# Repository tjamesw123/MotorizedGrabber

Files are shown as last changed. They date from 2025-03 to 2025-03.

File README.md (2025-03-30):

# MotorizedGrabber
3d models, custom circuit board, design and parts list for a motorized grabber design

# Grabber Shopping List

2 mm outer thickness with 22 mm inner diameter alumuinum pipe, 2 meters 

3d printer and filament, carbon fiber PLA was used for this grabber but normal PLA should still work with possibly some tweaks to the models or maybe non at all as Carbon Fiber PLA and PLA have similar print characteristics
(Note that a sleve was used for fitting the adapter to the alumnium grabber pipe better after the lathe was used to trim the part till it fit with the alumium pipe, there is almost certainly another way to fit the aluminum pipe and the part together without such equipment. I would suggest tuning the fitting parts of the prints inner and outer diameter sizes till you can print a part that fits well with the aluminium pipe without any trim)

Drill Batterys and Charger https://www.amazon.com/dp/B07X2V5116/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

Round Head Machine Screw, 8-32-Inch x 1-Inch, 2 of them https://www.amazon.com/dp/B00843ER7W?ref_=cm_sw_r_cp_ud_dp_5XYYPG3079ASXCVBMPT5

Small Screws https://www.amazon.com/dp/B078ZVLFWY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

Micro Limit Switch	https://www.amazon.com/dp/B07X142VGC/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 , I got the 10 pack of these but most limit switches will do as you only need one of them for the limiter

SPDT Push Button Switches https://www.digikey.com/en/products/detail/e-switch/700SP7B10M2QEH/502058 , I bought 4 when making it in case I messed up 2 but you only need 2 for the design

Custom Circuit Board for Grabber , The gerber files are in the repo, I used PCBWay for ordering the boards, you do have to mininum order 10 for 20 dollars but for this project it made soldering way easier and much more reliable then soldering directly to the pins.

A fair amount of 22 gage wire, I made an attempt at using quick connects to make the battery connection to the switches easier to disconnect but the current space issues make such things mildly difficult so you can just directly wire up the grabber and desolder for repairs. Annoying but with the space constraints it made sense at the time.

There are about 4 separate runs of wire you will have to run other then the wires built into the linear actuator
There are circuit diagrams that you can view from the photo section of the layout of the switch board or if you feel like not using it, it's going to tell you exactly how you have to run things.

Grabber 48"	https://www.amazon.com/dp/B000RUKZNU?ref=ppx_yo2ov_dt_b_fed_asin_title&th=1 , this is the grabber that you need to basically need to cut and then combined with the other parts in this design
Or
Grabber 36" https://www.amazon.com/dp/B0000V0AGS/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 , another grabber you can use if you want a shorter grabber for whatever reason, still works out the same for the most part

Battery Prongs	https://www.te.com/en/product-42214-2.html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 , I bought 4 again also because I wanted backups but you only need 2\

Micro Linear Actuator https://www.amazon.com/dp/B0B9JPQDSV?ref=ppx_yo2ov_dt_b_fed_asin_title&th=1, I bought 1 of these
(The gearing here is more aggressive then it needs to be on the 36" grabber but for the 48" it is required to get one of these as the gearing for a faster motor doesn't have enough static friction to keep the spring on the grabber from moving)

### An addendum on the PCB
You technically don't need this thing if your really determined but trust me when I say it really can be scuffed if you don't get this, if you are a beginner solderer I would recommend this and honestly even if your more experienced it just makes the whole circuit a lot neater. Having tiny 22 gage wires running inbetween the pins is messy, I rest my case. I have like 7 spares at this moment in time so if your really determined to not order a fresh batch you can attempt to reach out. The dupes also leave room for failures and they make for ok solder practice boards as well with the number of pins.

The spacing is also tiny there isn't a lot of room in the handle of the grabber so the board just made sense to keep things more neat

## Photos

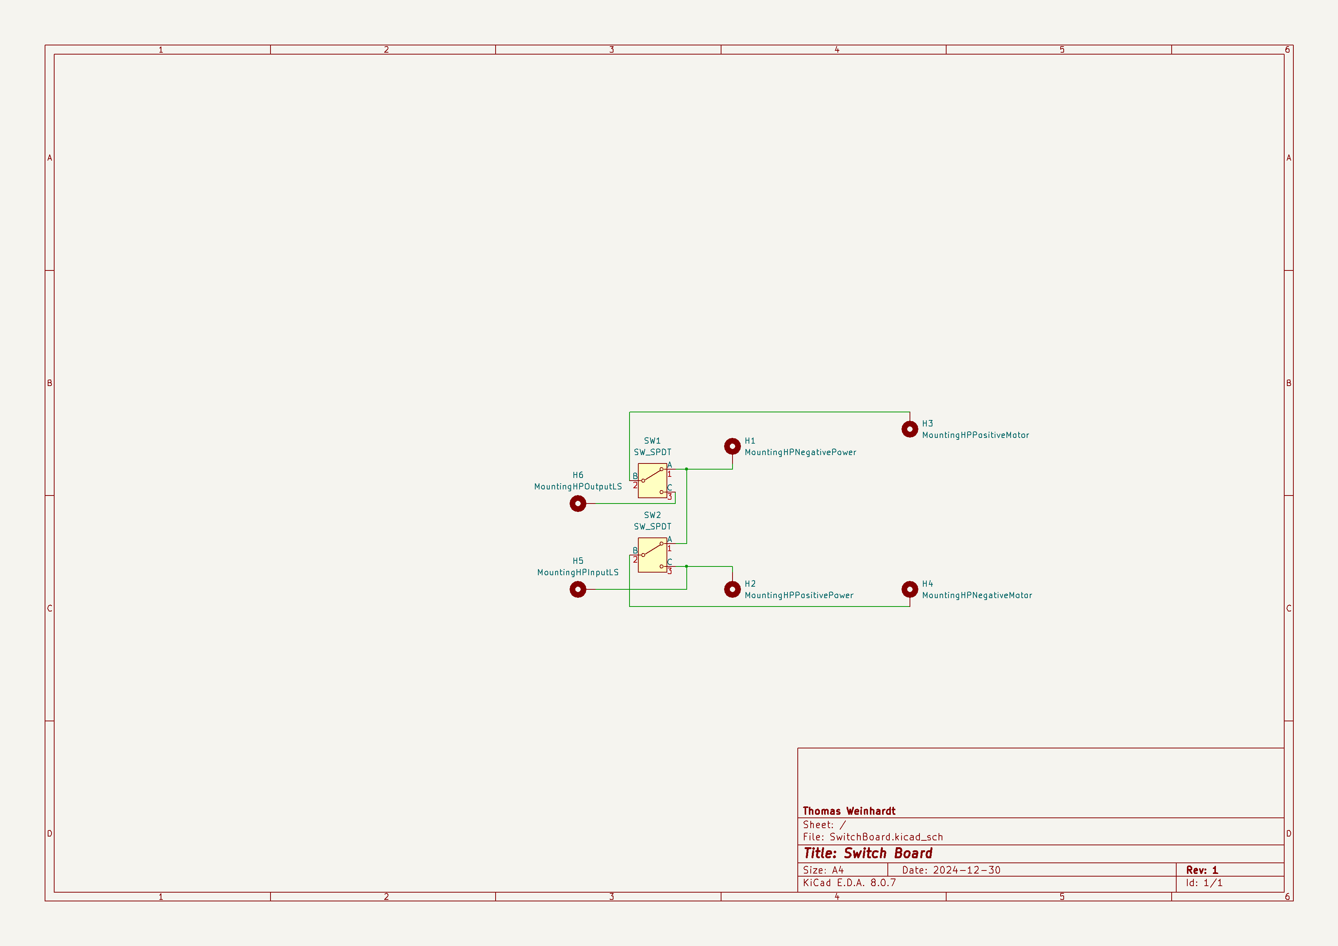
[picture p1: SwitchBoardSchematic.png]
Switch Board Schematic

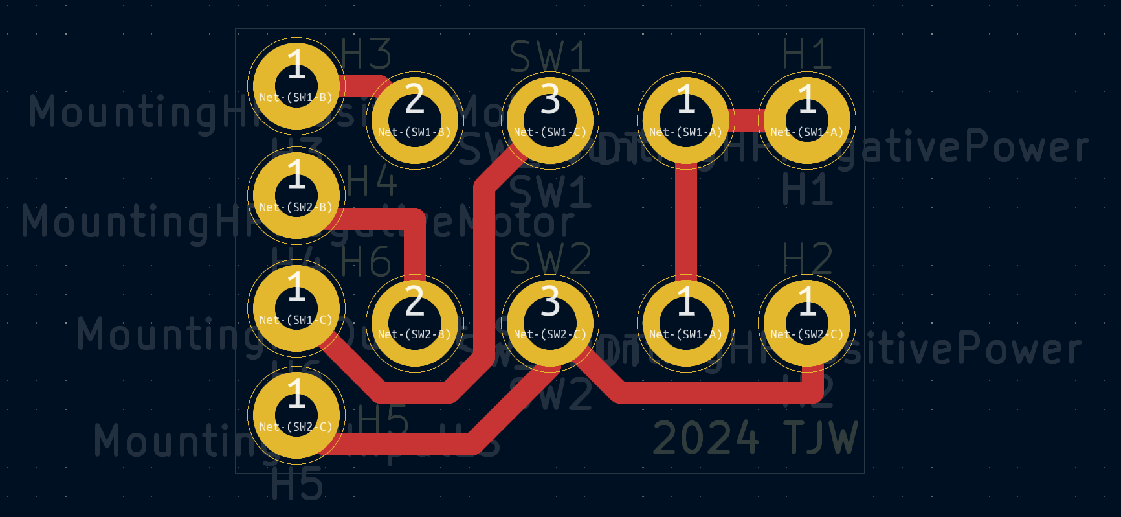
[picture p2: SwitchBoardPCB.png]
Switch Board PCB


(I used KiCAD for the board designing program)
[GerbersAndProductionFiles](SwitchBoard/pcbway_production)
Also use the settings listed in the [GrabberPCBSpecs](GrabberPCBSpecs.pdf)

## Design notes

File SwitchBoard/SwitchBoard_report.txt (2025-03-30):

PCB statistics report
=====================
- Date: 12/30/2024 1:51:36 PM
- Project: SwitchBoard
- Board name: SwitchBoard

Board
-----
- Width: 22.0000 mm
- Height: 15.4000 mm
- Area: 338.8000 mm²

Pads
----
- Through hole: 6
- SMD: 6
- Connector: 0
- NPTH: 0

Vias
----
- Through vias: 0
- Blind/buried: 0
- Micro vias: 0

Components
----------

| | Front Side | Back Side | Total |
|---|---|---|---|
|THT: | 8 | 0 | 8 |
|SMD: | 0 | 0 | 0 |
|Unspecified:  | 0 | 0 | 0 |
|Total: | 8 | 0 | 8 |

Drill holes
-----------

| Count | Shape | X Size | Y Size | Plated | Via/Pad | Start Layer | Stop Layer |
|---|---|---|---|---|---|---|---|
| 6 | Round | 1.8500 mm | 1.8500 mm | PTH | Pad | F.Cu | B.Cu |

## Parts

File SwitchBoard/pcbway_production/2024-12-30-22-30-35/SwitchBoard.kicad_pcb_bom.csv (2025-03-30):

Designator | Quantity | Value | Footprint | Package | MPN | DNP | Mount_Type | Description
SW1, SW2 | 2 | SW_SPDT | SP-7 |  |  |  | tht | Switch, single pole double throw

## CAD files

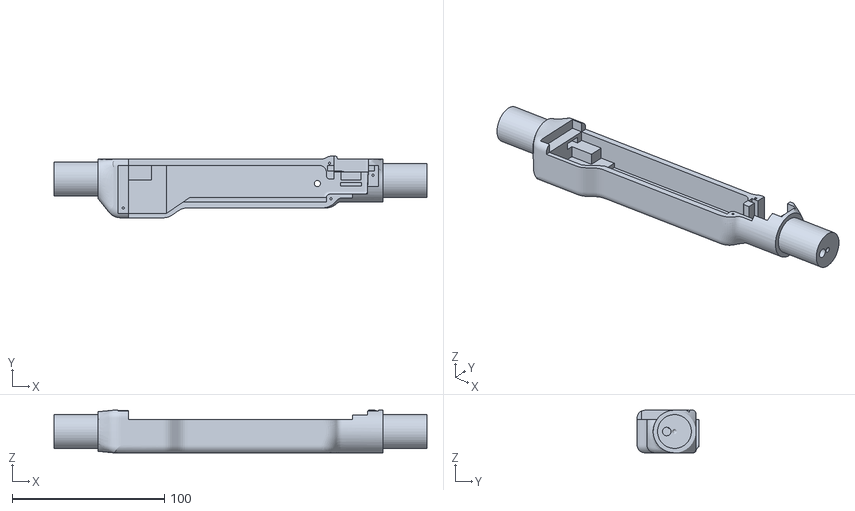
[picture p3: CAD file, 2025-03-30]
PartsFolder/GrabberCasingMain.stl
244.9 x 40.5 x 28.0

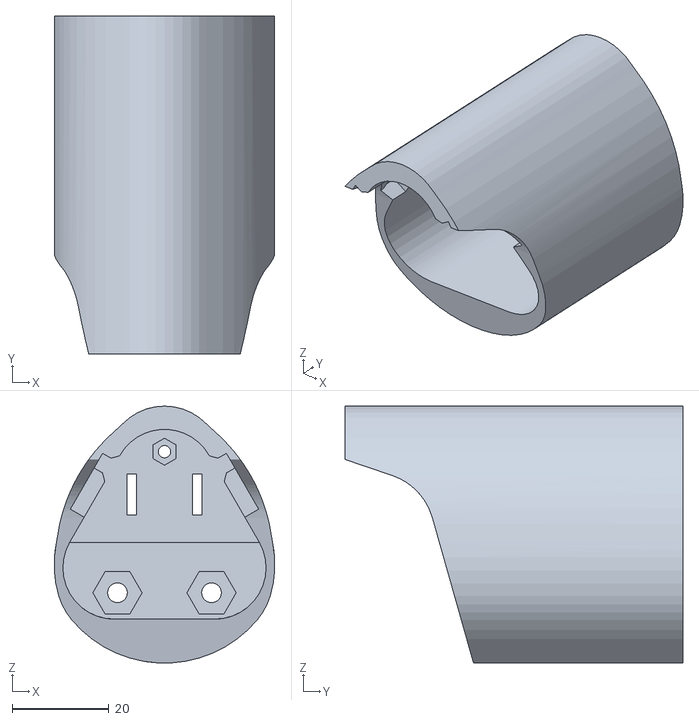
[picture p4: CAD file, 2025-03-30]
PartsFolder/GrabberBatteryHolder.stl
45.5 x 69.7 x 53.0

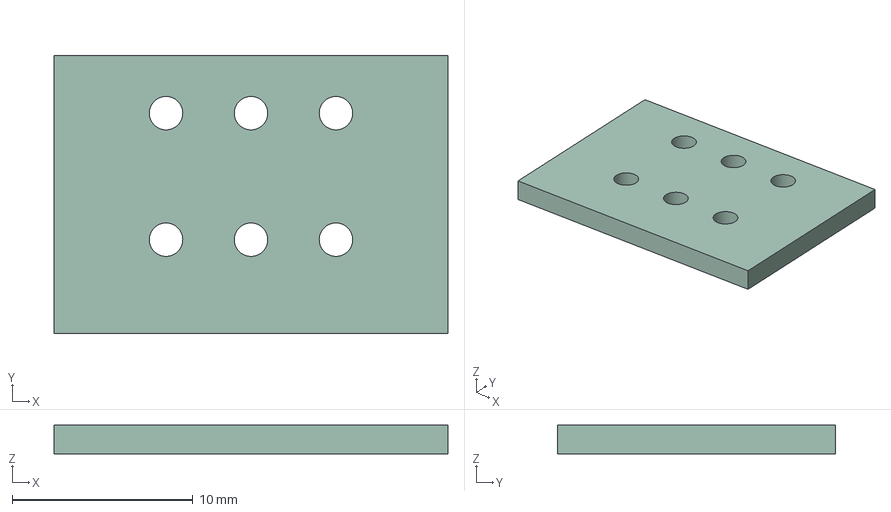
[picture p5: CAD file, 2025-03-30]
SwitchBoard/SwitchBoard.step
21.8 x 15.4 x 1.60 mm

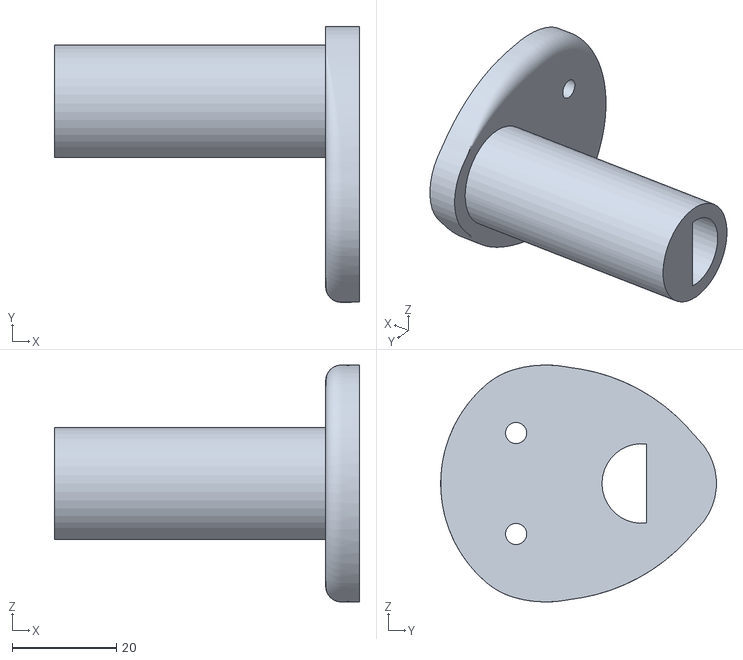
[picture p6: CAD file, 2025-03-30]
PartsFolder/GrabberBatteryCap.stl
58.6 x 53.0 x 45.5

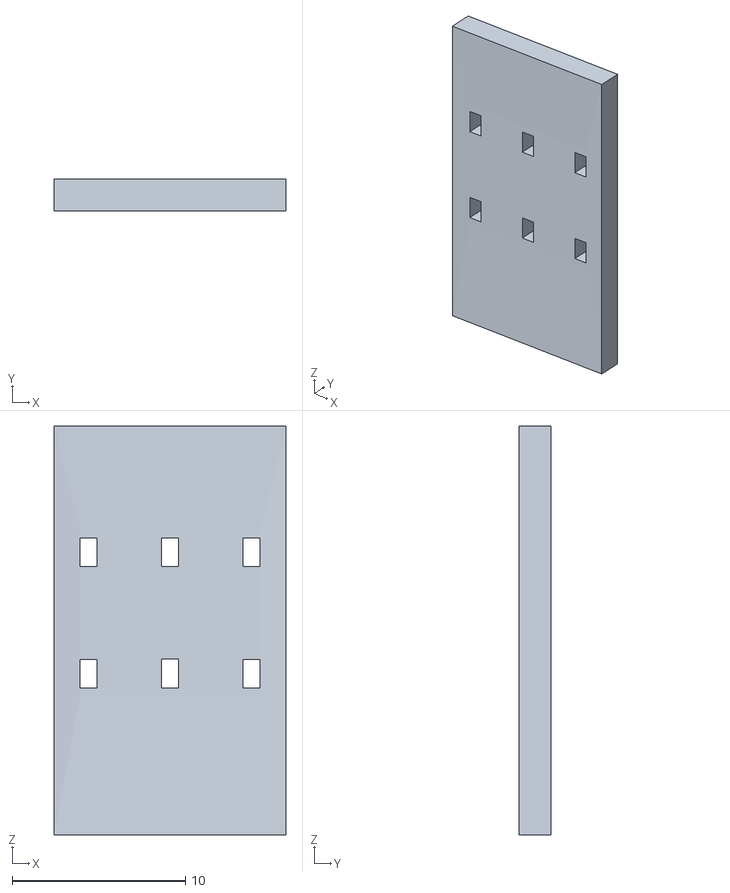
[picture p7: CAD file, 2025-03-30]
PartsFolder/GrabberButtonPlatform.stl
13.4 x 1.82 x 23.6

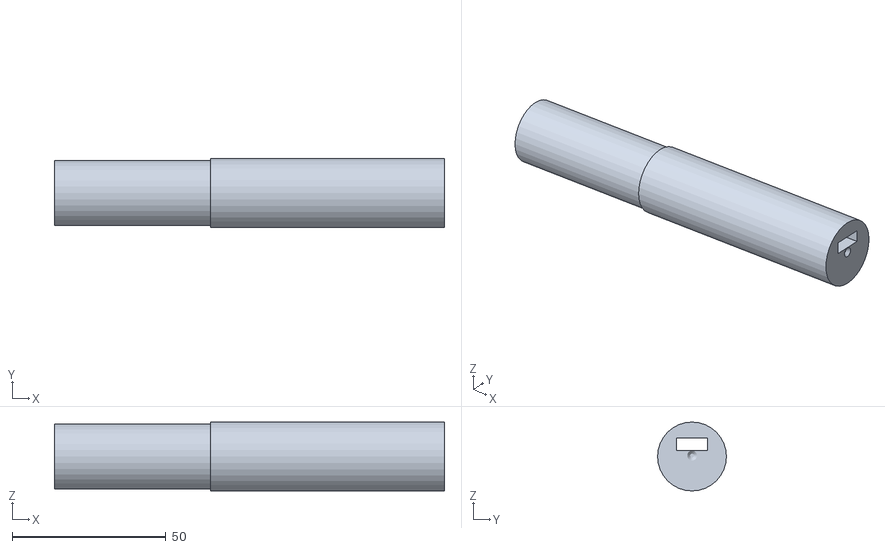
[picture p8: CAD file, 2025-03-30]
PartsFolder/GrabberPipeAdapter.stl
127.0 x 22.4 x 22.4

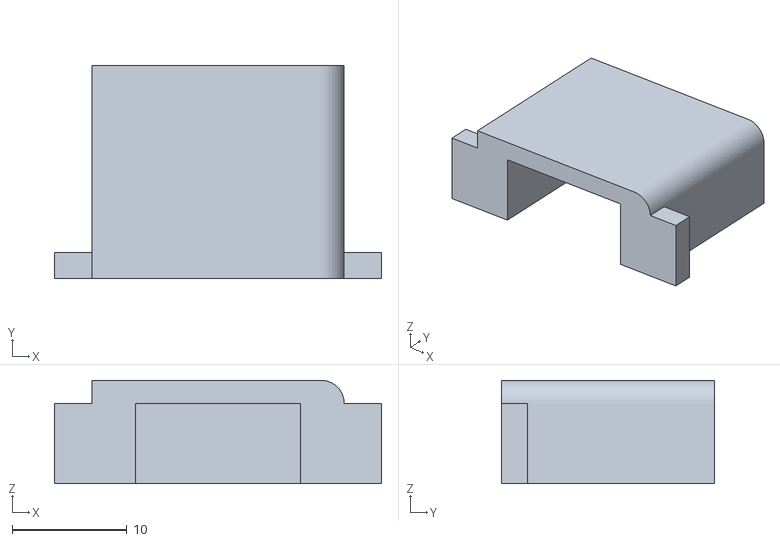
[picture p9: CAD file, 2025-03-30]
PartsFolder/GrabberLeftButtonCap.stl
28.5 x 18.5 x 9.00

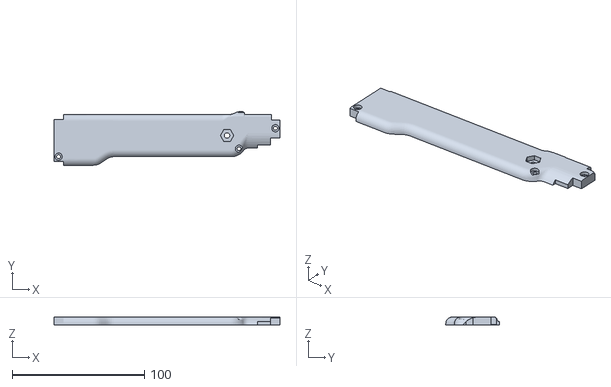
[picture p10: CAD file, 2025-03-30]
PartsFolder/GrabberCasingCover.stl
171.0 x 40.5 x 6.00

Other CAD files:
PartsFolder/GrabberRightButtonCap.stl
BlenderFile/GrabberCasing.blend

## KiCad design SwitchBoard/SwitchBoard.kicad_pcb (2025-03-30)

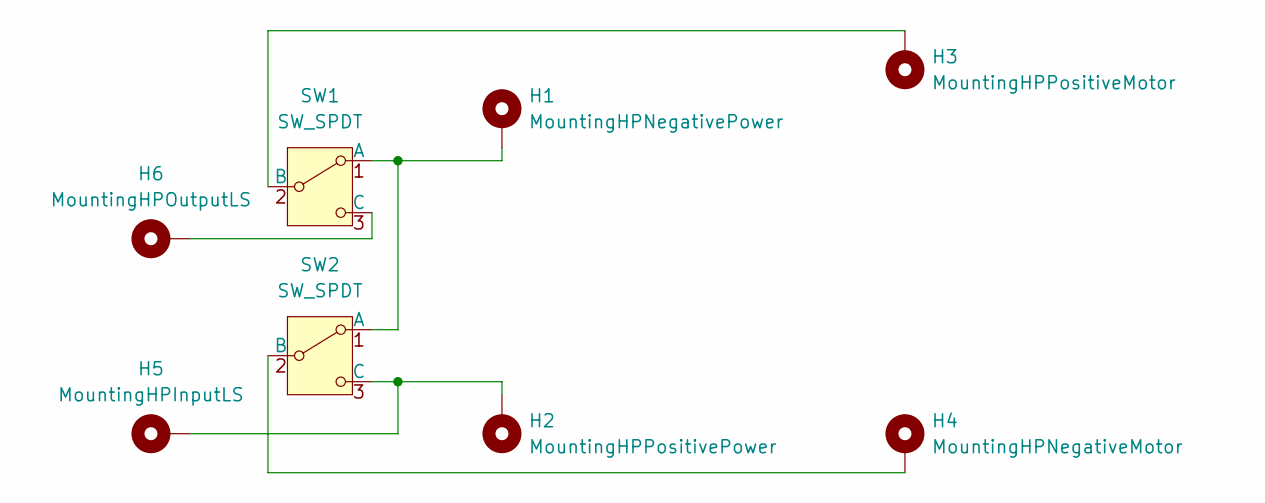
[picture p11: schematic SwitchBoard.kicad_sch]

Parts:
H1: MountingHPNegativePower; SmallerPad
H2: MountingHPPositivePower; SmallerPad
H3: MountingHPPositiveMotor; SmallerPad
H4: MountingHPNegativeMotor; SmallerPad
H5: MountingHPInputLS; SmallerPad
H6: MountingHPOutputLS; SmallerPad
SW1, SW2: SW_SPDT; SP-7

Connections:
unnamed: H1.1, SW1.1 (A), SW2.1 (A)
unnamed: H3.1, SW1.2 (B)
unnamed: H6.1, SW1.3 (C)
unnamed: H4.1, SW2.2 (B)
unnamed: H2.1, H5.1, SW2.3 (C)

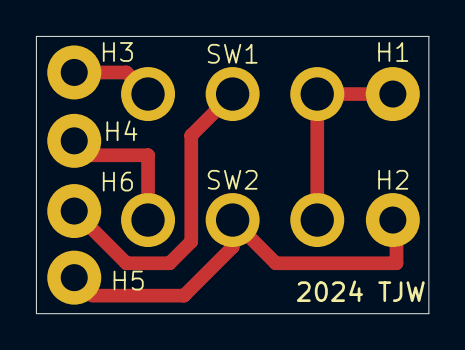
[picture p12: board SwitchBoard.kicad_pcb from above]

Board: 2 copper layers, 21.8 x 15.4 mm, 8 parts (0 on the bottom side), 5 nets.

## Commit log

2025-03-30 Added resources
    [GrabberBatteryCap.stl, GrabberBatteryHolder.stl, GrabberButtonPlatform.stl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]
2025-03-30 Updated README.md, and started adding things in
    [SwitchBoard.kicad_sch]
2025-03-30 Reorganized stls and blender files
    [GrabberBatteryCap.stl, GrabberBatteryHolder.stl, GrabberButtonPlatform.stl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]
